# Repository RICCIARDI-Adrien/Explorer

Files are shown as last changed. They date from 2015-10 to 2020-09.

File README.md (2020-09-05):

# Explorer

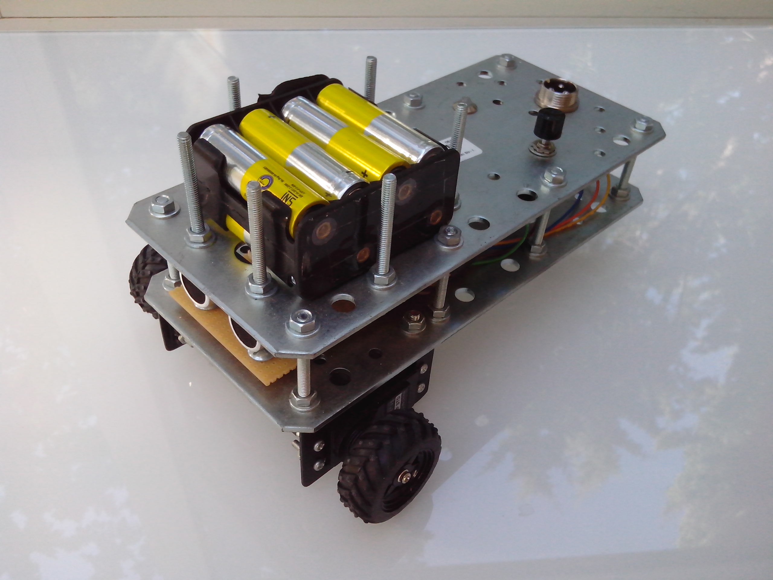
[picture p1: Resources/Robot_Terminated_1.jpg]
Robot terminated 1


A small wheeled robot based on a PIC18F26K22 microcontroller and a single ultrasonic distance sensor.  
The goal was to develop and test two basic artificial intelligence algorithms, both relying only on the ultrasonic sensor :
- The robot moves at will in a room and must avoid obstacles. It must never remain stuck.
- The robot is idle, waiting for a moving object to come close to it. Then, it must follow the moving object, staying at a safe distance. If the moving object comes too close from the robot, the robot must escape.

## Hardware
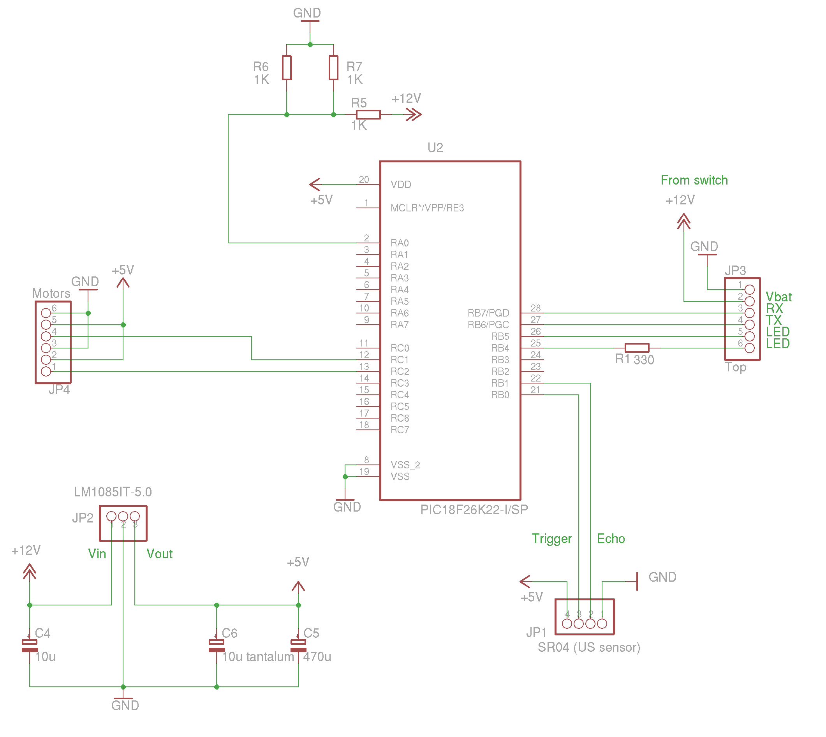
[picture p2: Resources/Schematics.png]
Main board schematics


## Build tools
The schematics and PCB were drawn using Cadsoft Eagle 6.6.0.  
The microcontroller firmware is built with SourceBoost 7.30.  
The Command Line Interface program can be built under Linux using gcc or under Windows with Cygwin or MinGW.

## Photo gallery

### Chassis construction

Start with two 200x90x2mm galvanized steel plates :
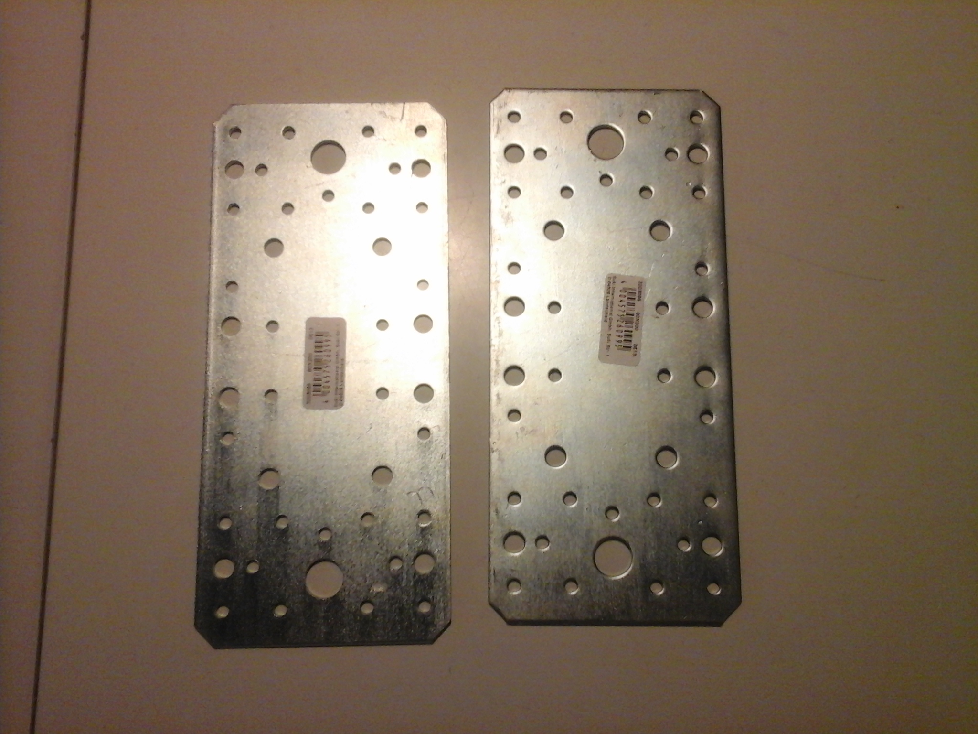
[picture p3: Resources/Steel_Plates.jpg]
Steel plates


One plate will be the chassis bottom. Make holes for servomotor support flat angle brackets and screw them :
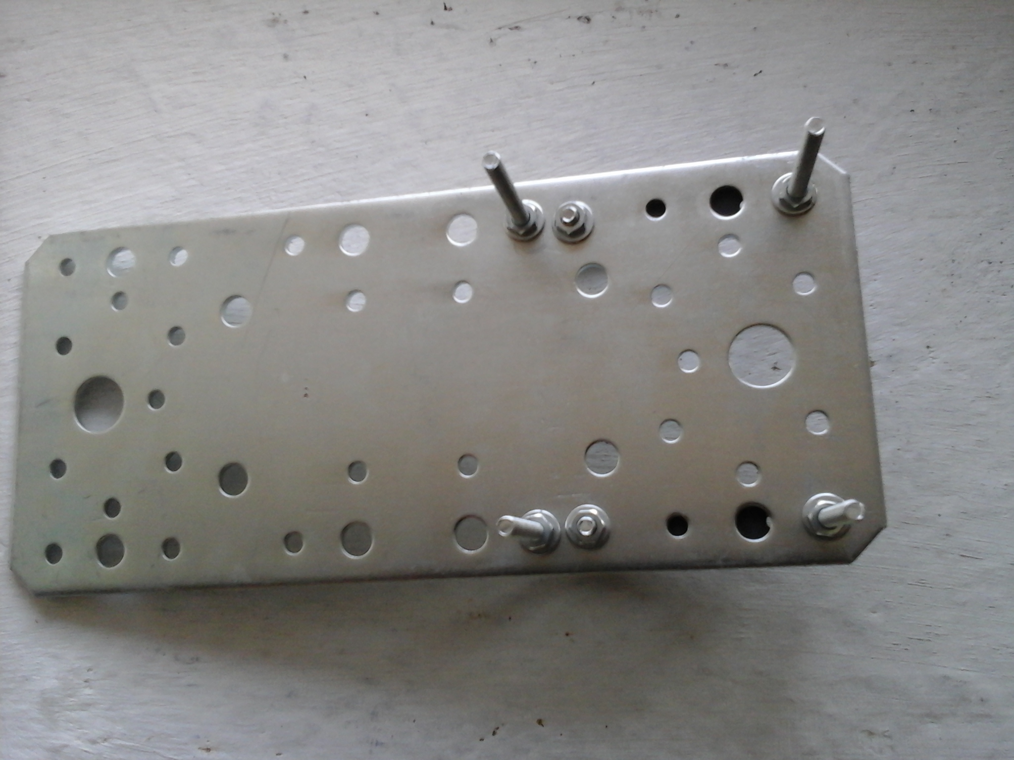
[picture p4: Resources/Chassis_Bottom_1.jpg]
Chassis bottom 1


Here is the other side :
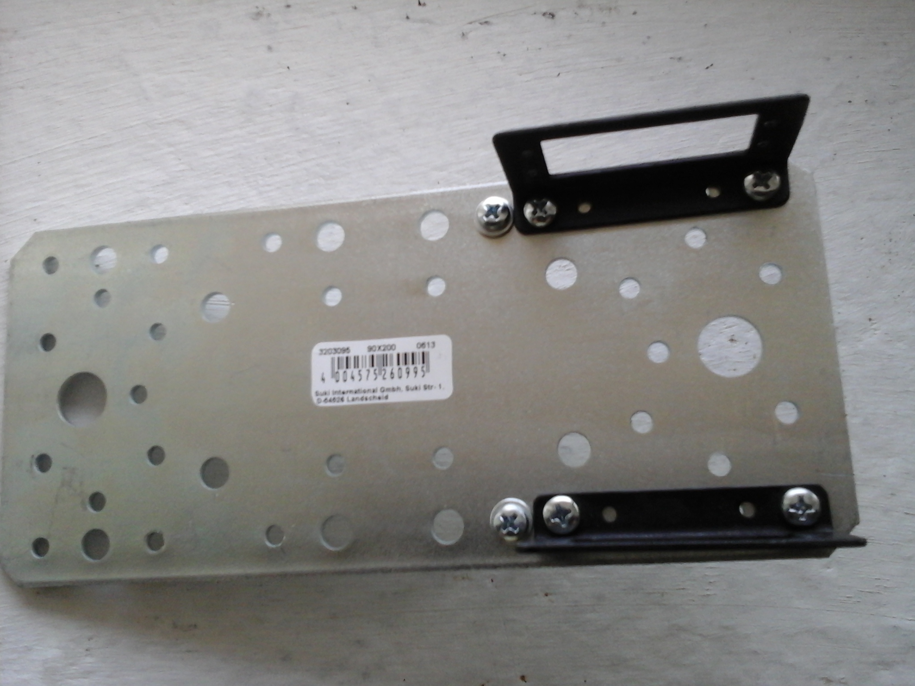
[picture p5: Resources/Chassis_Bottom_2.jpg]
Chassis bottom 2


Now screw the free wheel :
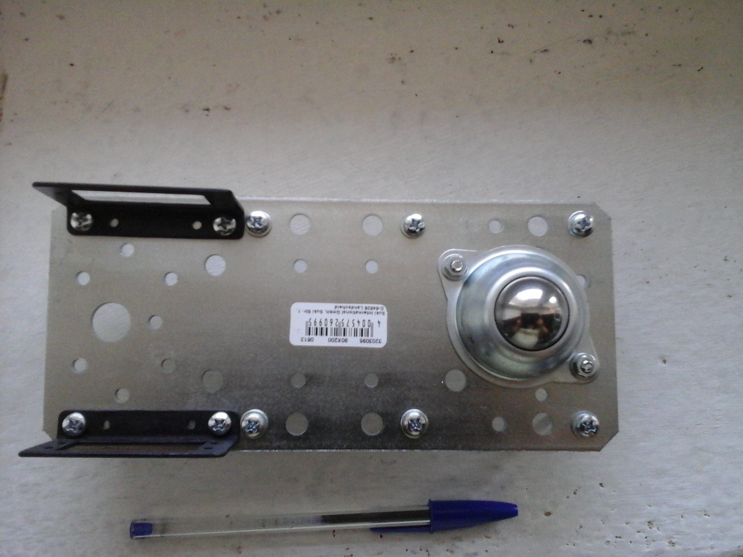
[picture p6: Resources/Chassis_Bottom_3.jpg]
Chassis bottom 3


Add the screws that will hold the chassis upper plate :
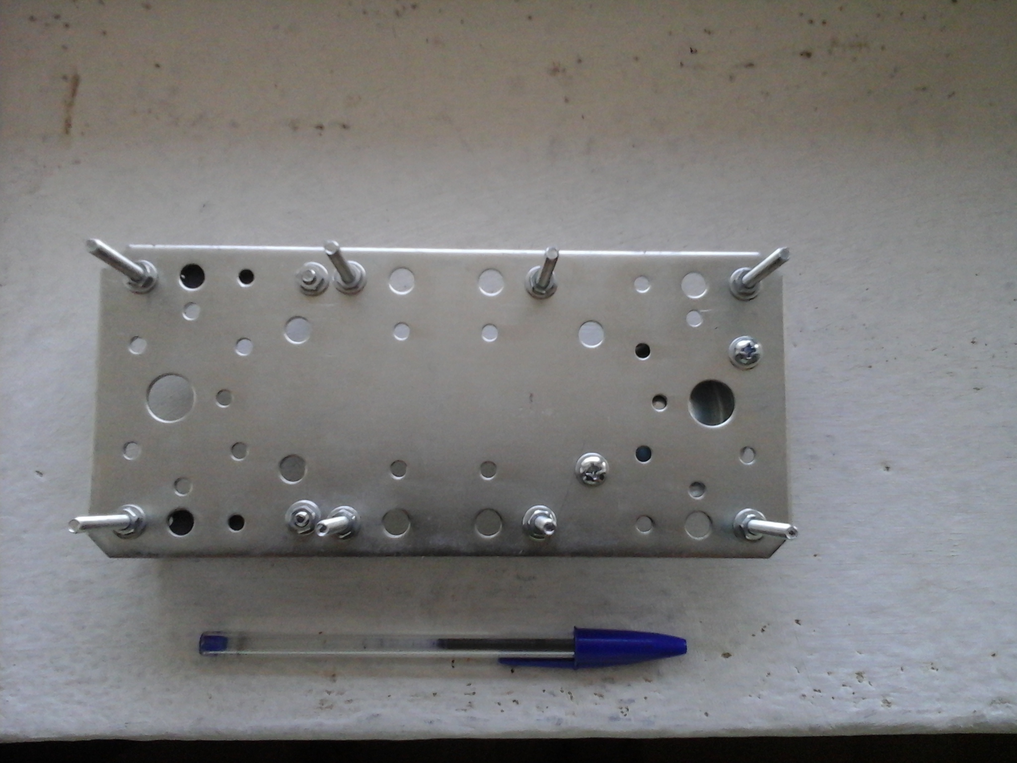
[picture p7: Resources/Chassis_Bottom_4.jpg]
Chassis bottom 4


### Motors assembly

Here are the servomotors :
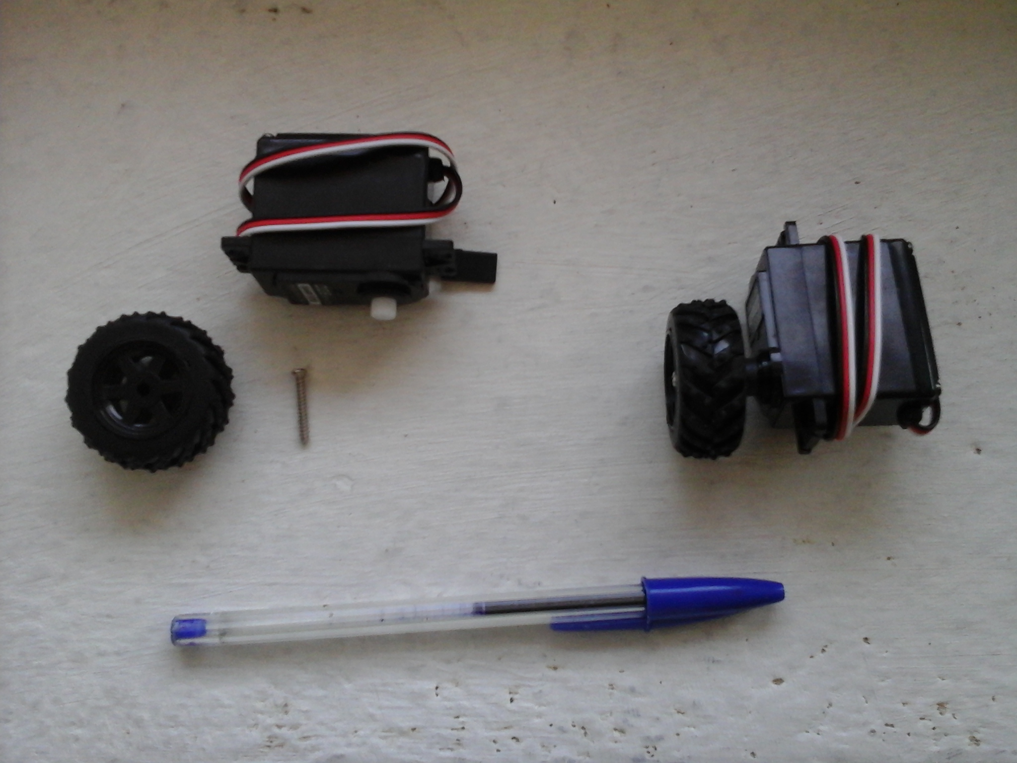
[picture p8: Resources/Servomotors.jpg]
Servomotors


Screw them into supports :
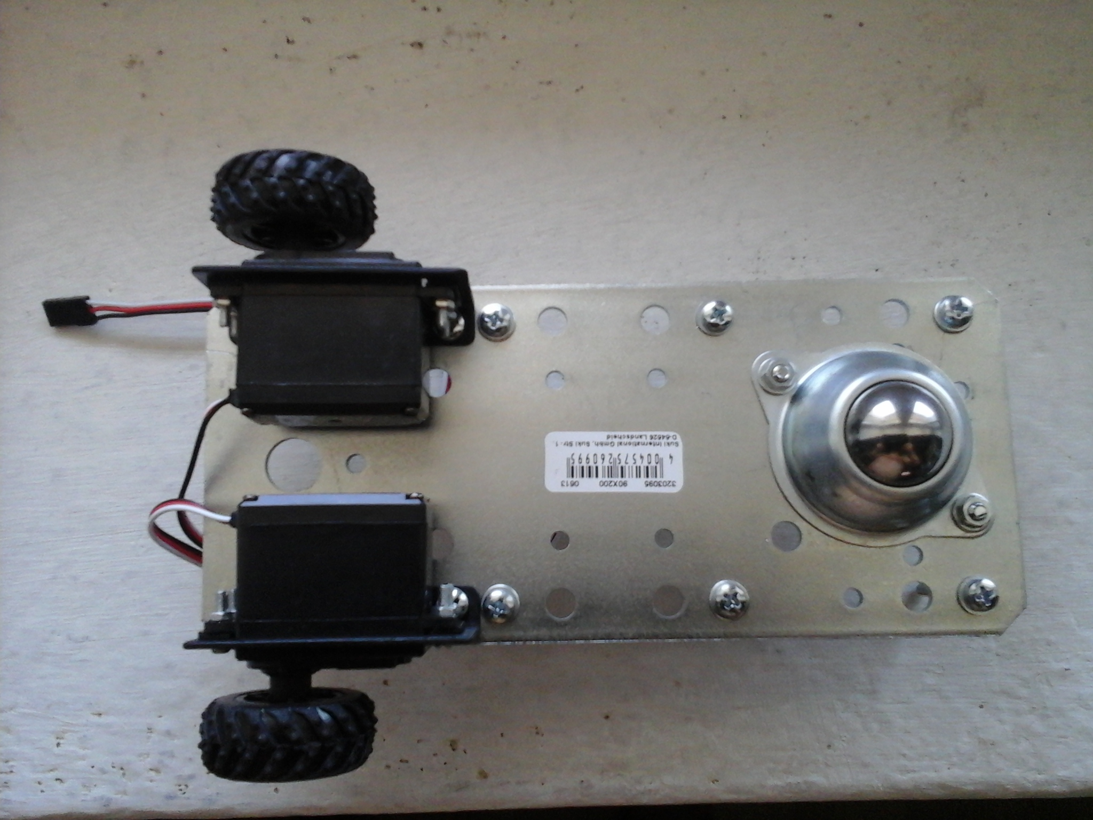
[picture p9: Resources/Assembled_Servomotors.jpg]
Assembled servomotors


### Voltage regulator assembly

Screw voltage regulator to chassis bottom plate. This allows to use the whole chassis as heat sink.
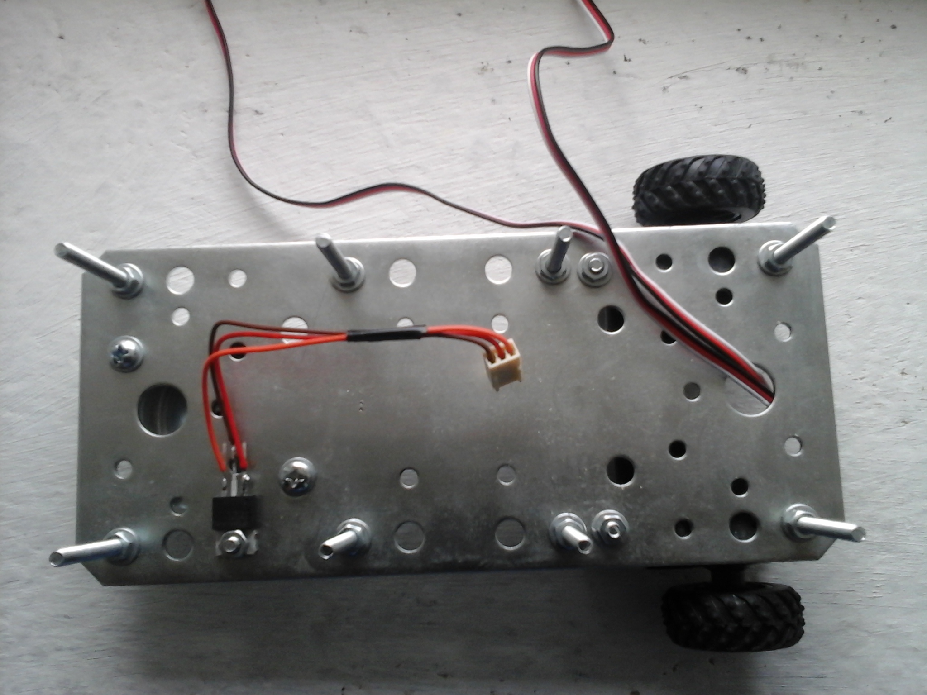
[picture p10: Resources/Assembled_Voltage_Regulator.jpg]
Assembled voltage regulator


### Chassis upper part

Drill holes for LED, switch and serial communication connector, then screw them. Also add the nuts and bolts that will hold the battery pack.
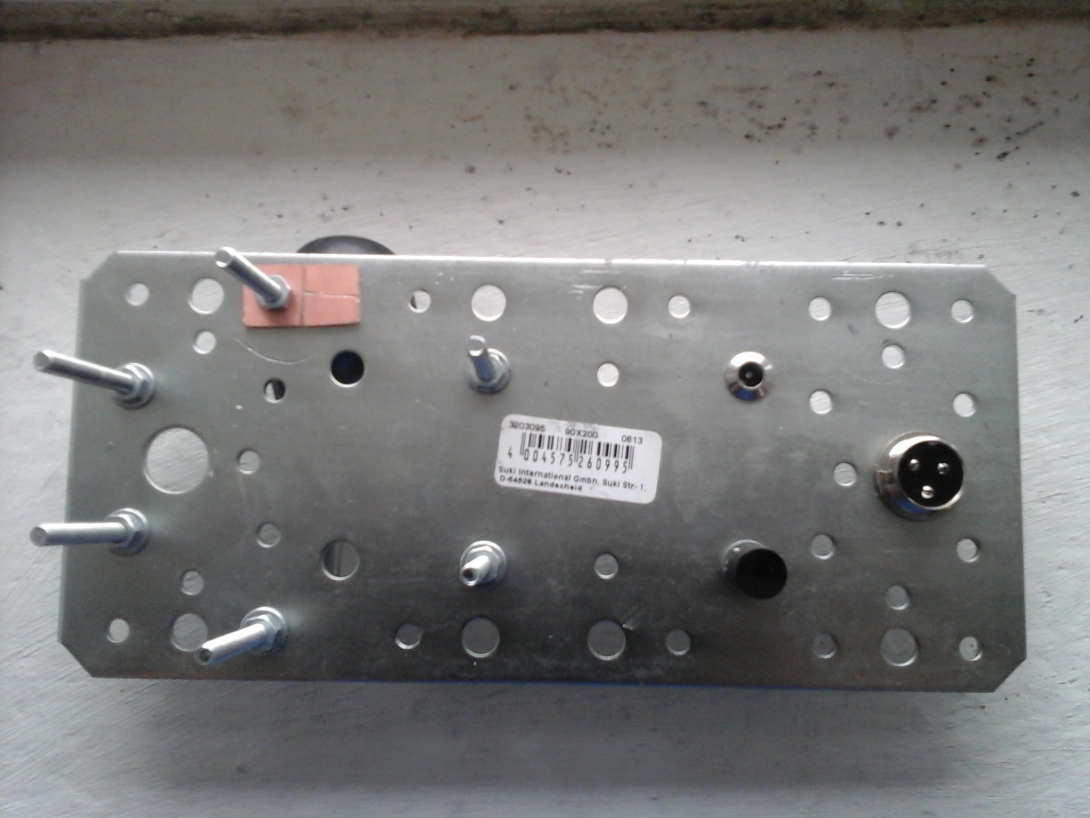
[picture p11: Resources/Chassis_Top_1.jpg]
Chassis top 1


Solder battery pack coupler to a little piece of PCB (don't forget to isolate terminals). This way, when coupler wires will break (it just a matter of time before it happens), it is easy to repair without having to disassemble the chassis.
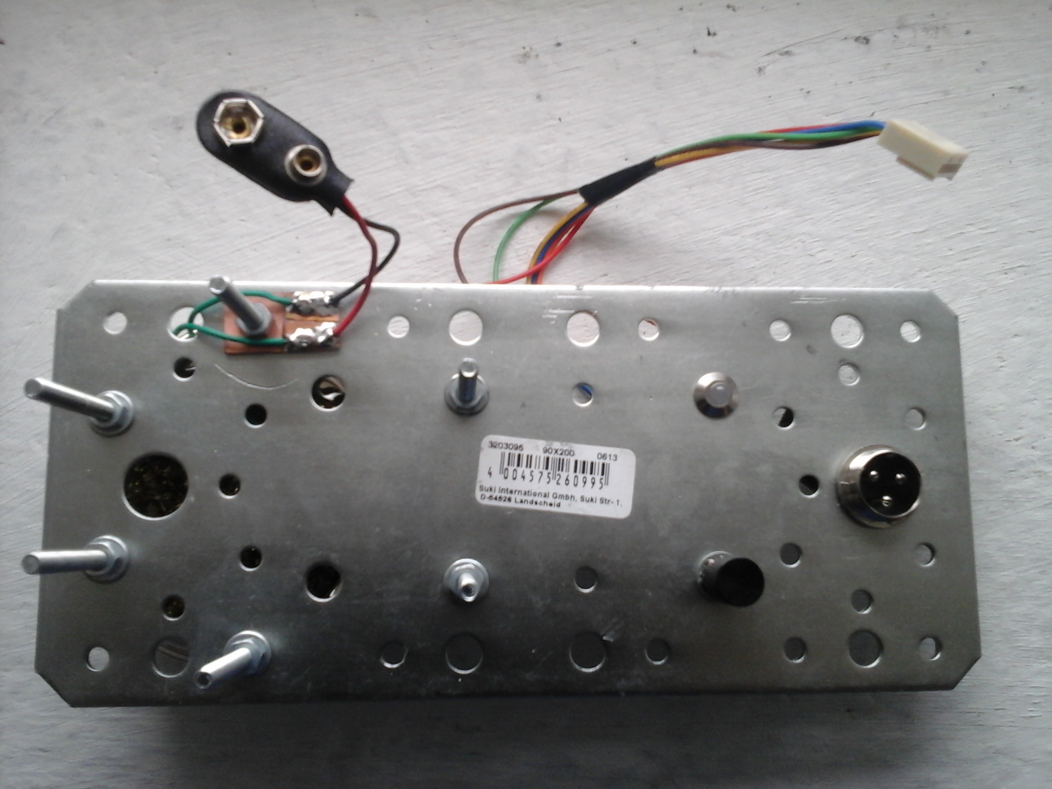
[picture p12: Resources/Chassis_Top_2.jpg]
Chassis top 2


Solder LED, switch and connector wires :
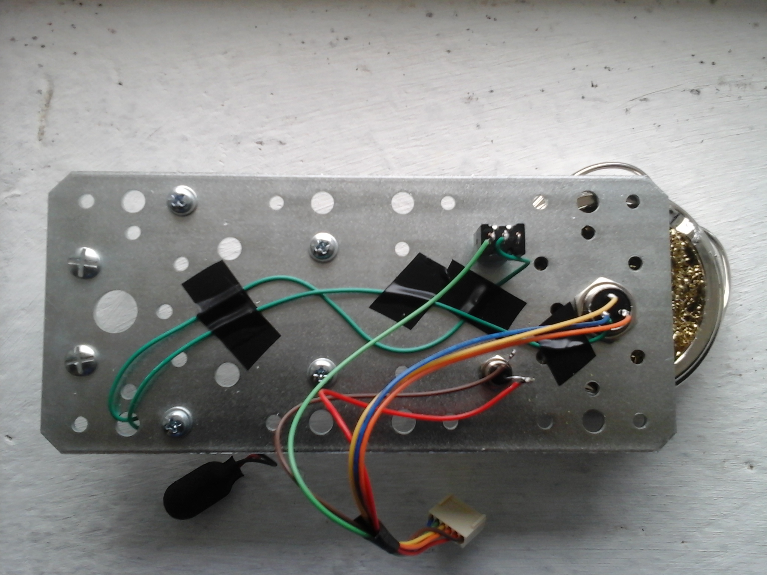
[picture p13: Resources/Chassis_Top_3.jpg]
Chassis top 3


### Electronic board

Board is made of test PCB soldered by hand.
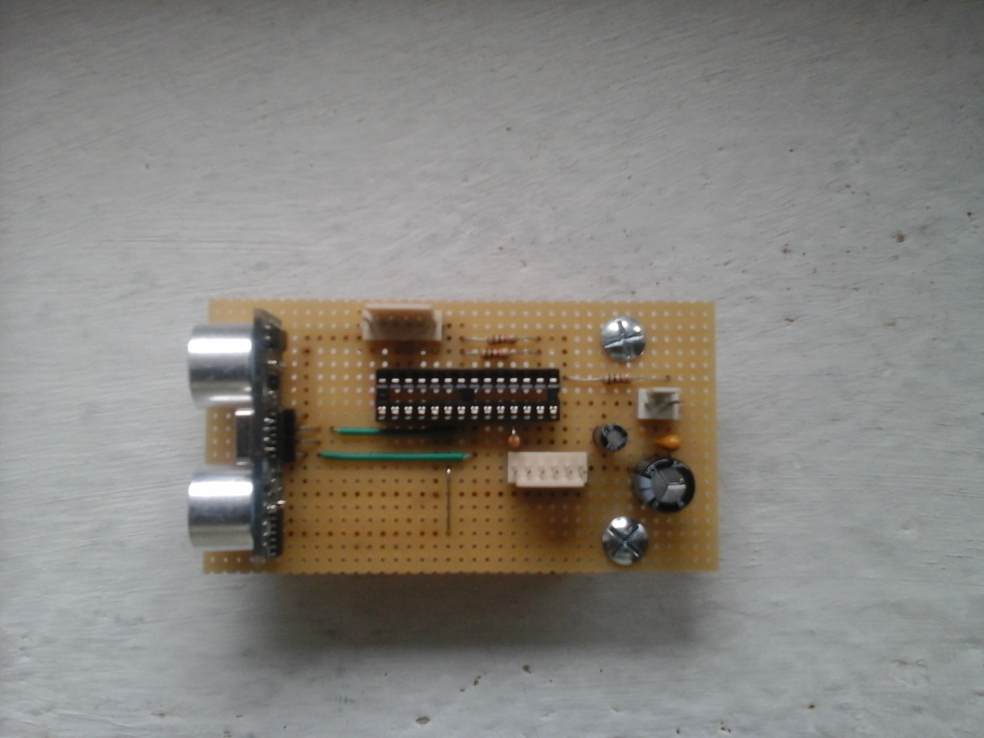
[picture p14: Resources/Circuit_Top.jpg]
Circuit top

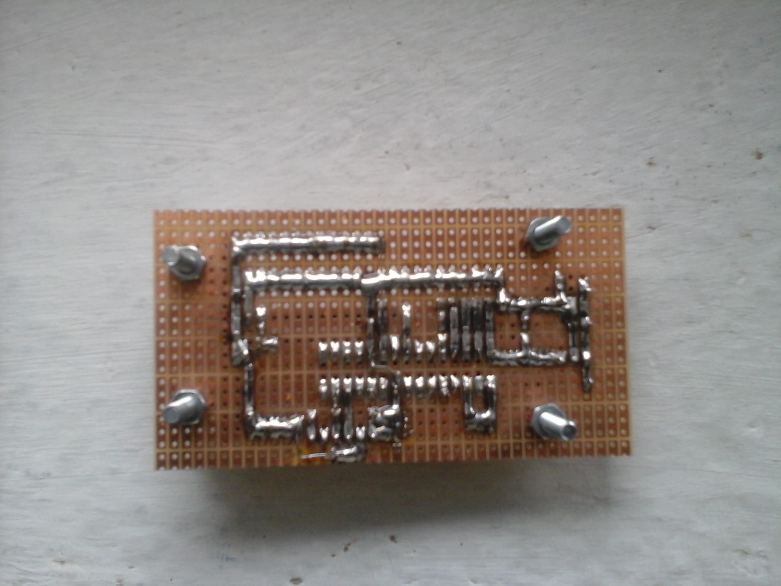
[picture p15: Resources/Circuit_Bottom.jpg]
Circuit bottom


Here is the board screwed to the chassis bottom :
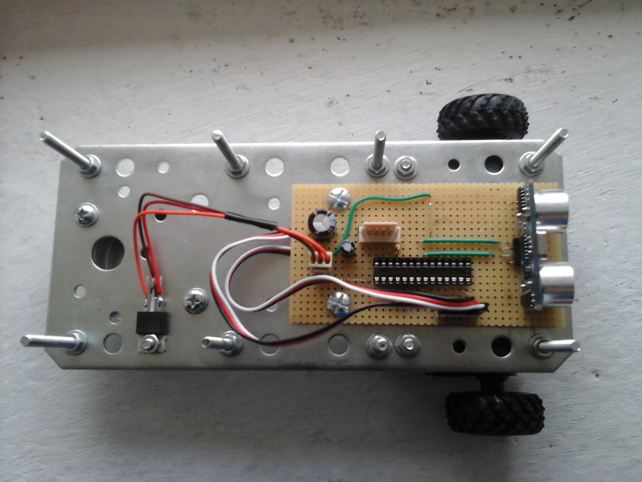
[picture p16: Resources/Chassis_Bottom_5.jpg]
Chassis bottom 5


### Fully assembled robot

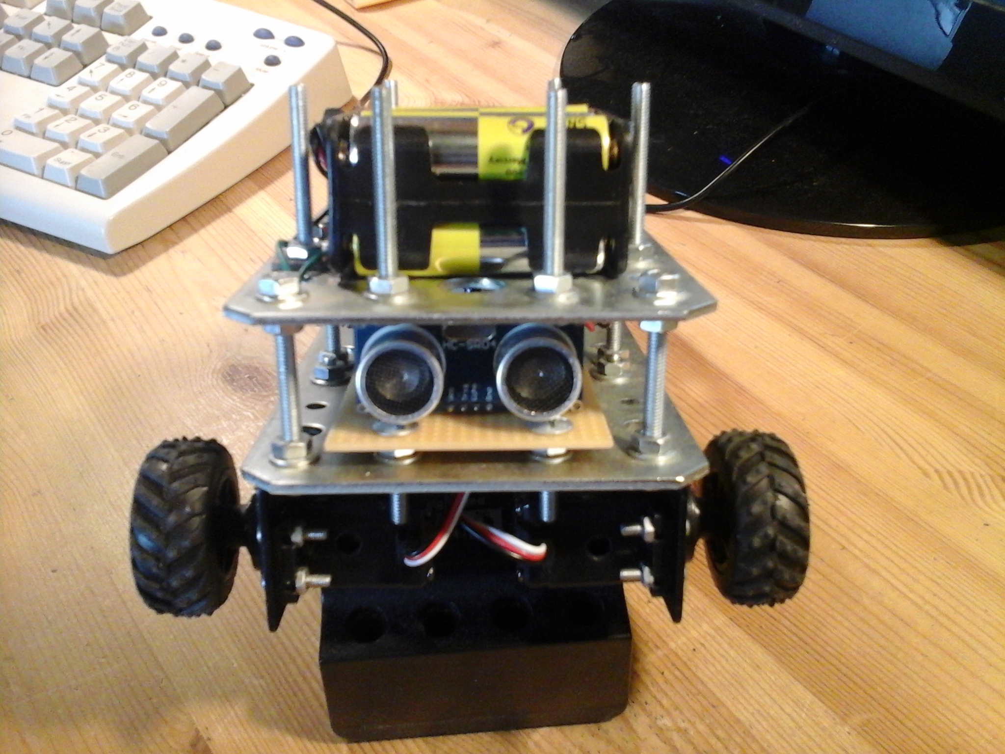
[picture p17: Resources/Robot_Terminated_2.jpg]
Robot terminated 2

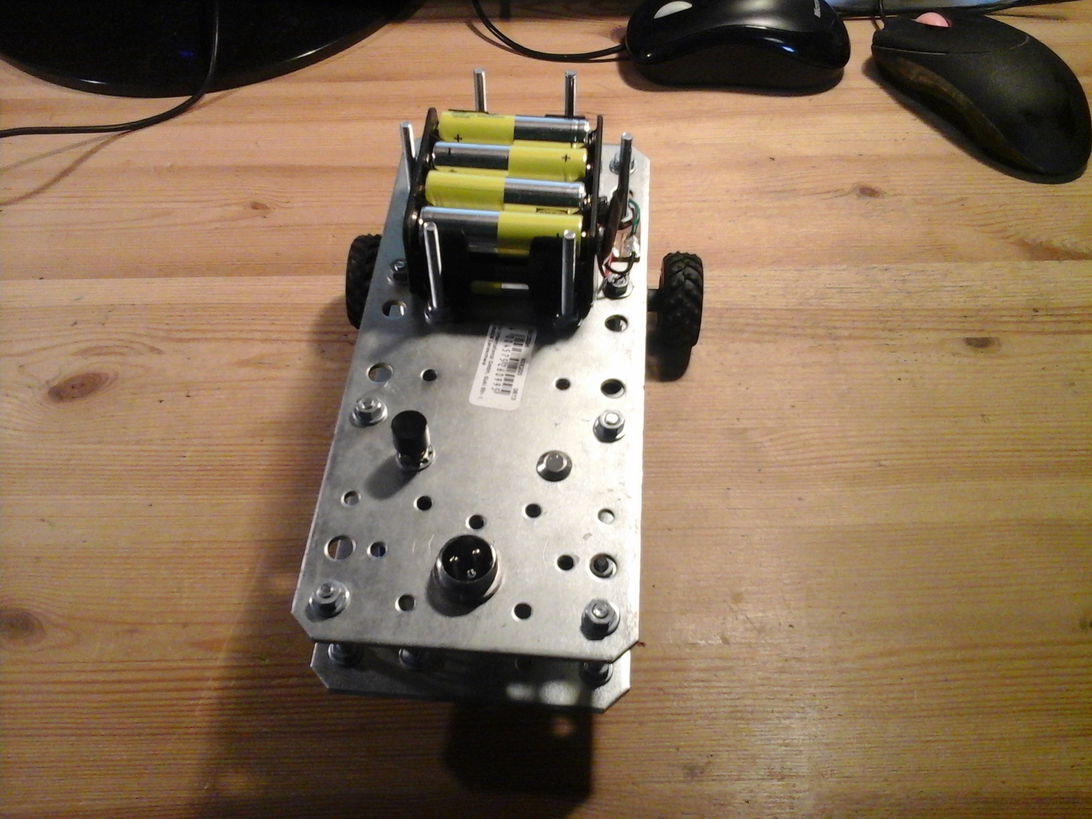
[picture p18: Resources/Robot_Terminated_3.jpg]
Robot terminated 3

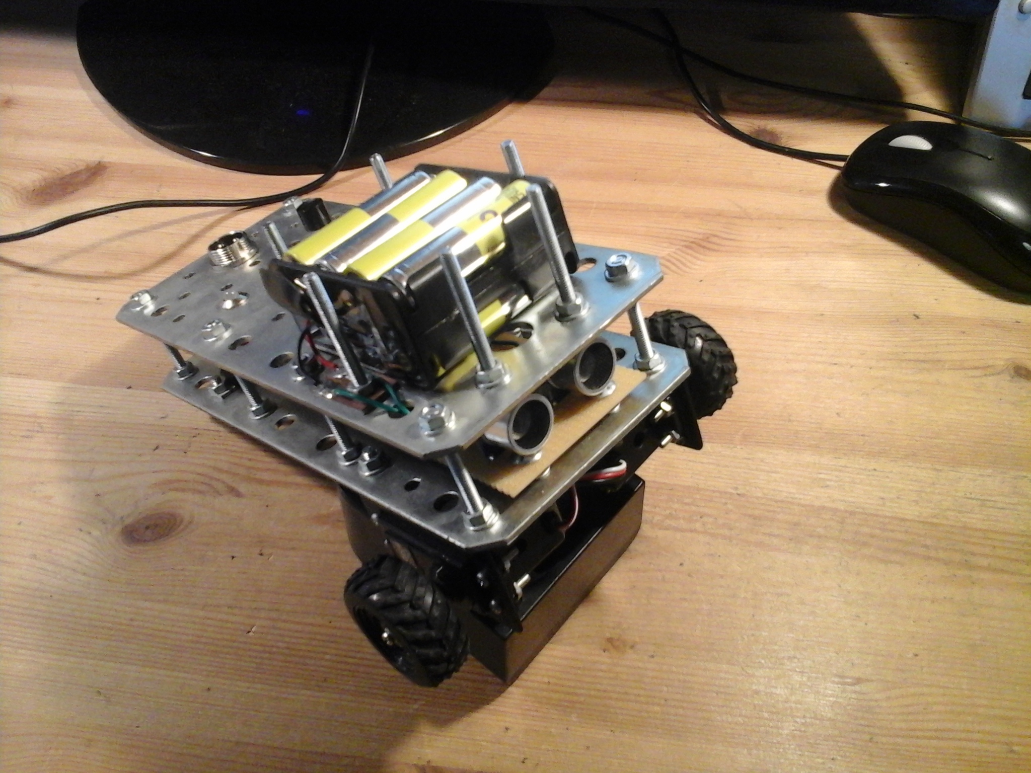
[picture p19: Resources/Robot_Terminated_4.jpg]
Robot terminated 4


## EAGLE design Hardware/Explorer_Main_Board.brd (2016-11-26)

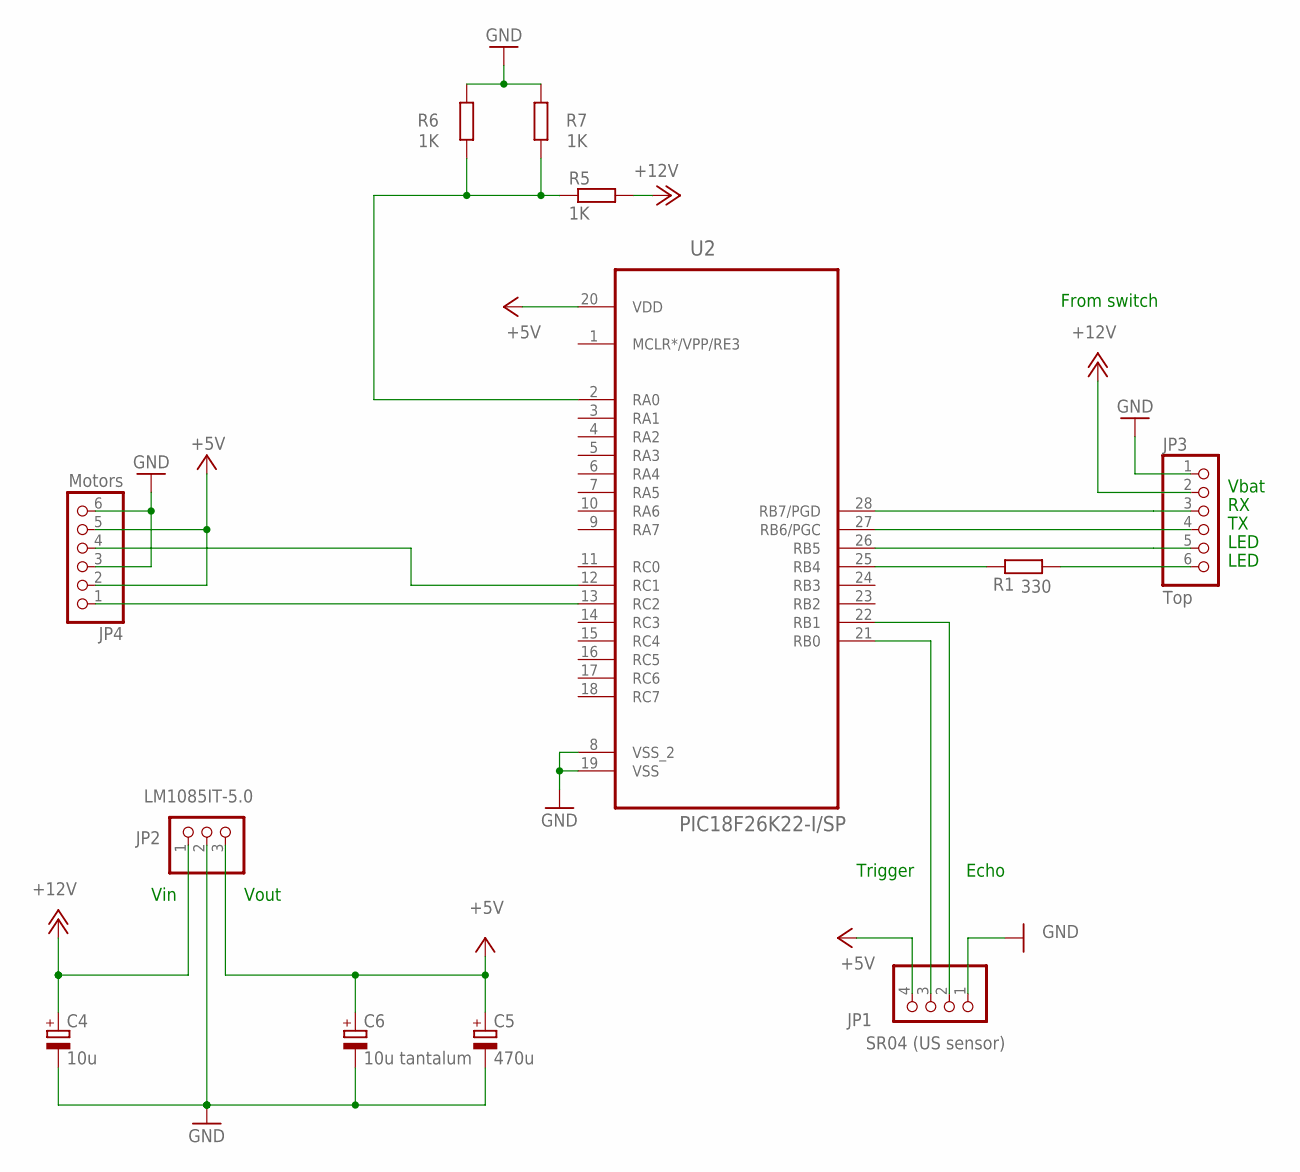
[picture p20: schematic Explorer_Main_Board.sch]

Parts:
C4: 10u; E2,5-6E
C5: 470u; E5-8,5
C6: 10u tantalum; E2,5-6E
JP1: SR04 (US sensor); 1X04
JP2: LM1085IT-5.0; 1X03
JP3: Top; 1X06
JP4: Motors; 1X06
R1: 330; 0207/12
R5, R6, R7: 1K; 0207/12
U2: PIC18F26K22-I/SP; DIP254P762X508-28P

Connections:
+5V: C5.+, C6.+, JP1.4, JP2.3, JP4.2, JP4.5, U2.20 (VDD)
+12V: C4.+, JP2.1, JP3.2, R5.2
GND: C4.-, C5.-, C6.-, JP1.1, JP2.2, JP3.1, JP4.3, JP4.6, R6.2, R7.2, U2.8 (VSS_2), U2.19 (VSS)
unnamed: JP3.6, R1.1
unnamed: R1.2, U2.25 (RB4)
unnamed: JP1.2, U2.22 (RB1)
unnamed: JP1.3, U2.21 (RB0)
unnamed: R5.1, R6.1, R7.1, U2.2 (RA0)
unnamed: JP3.3, U2.28 (RB7/PGD)
unnamed: JP3.4, U2.27 (RB6/PGC)
unnamed: JP4.4, U2.12 (RC1)
unnamed: JP4.1, U2.13 (RC2)
unnamed: JP3.5, U2.26 (RB5)

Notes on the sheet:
Vbat
From switch
LED
Vin
Vout
Echo
Trigger

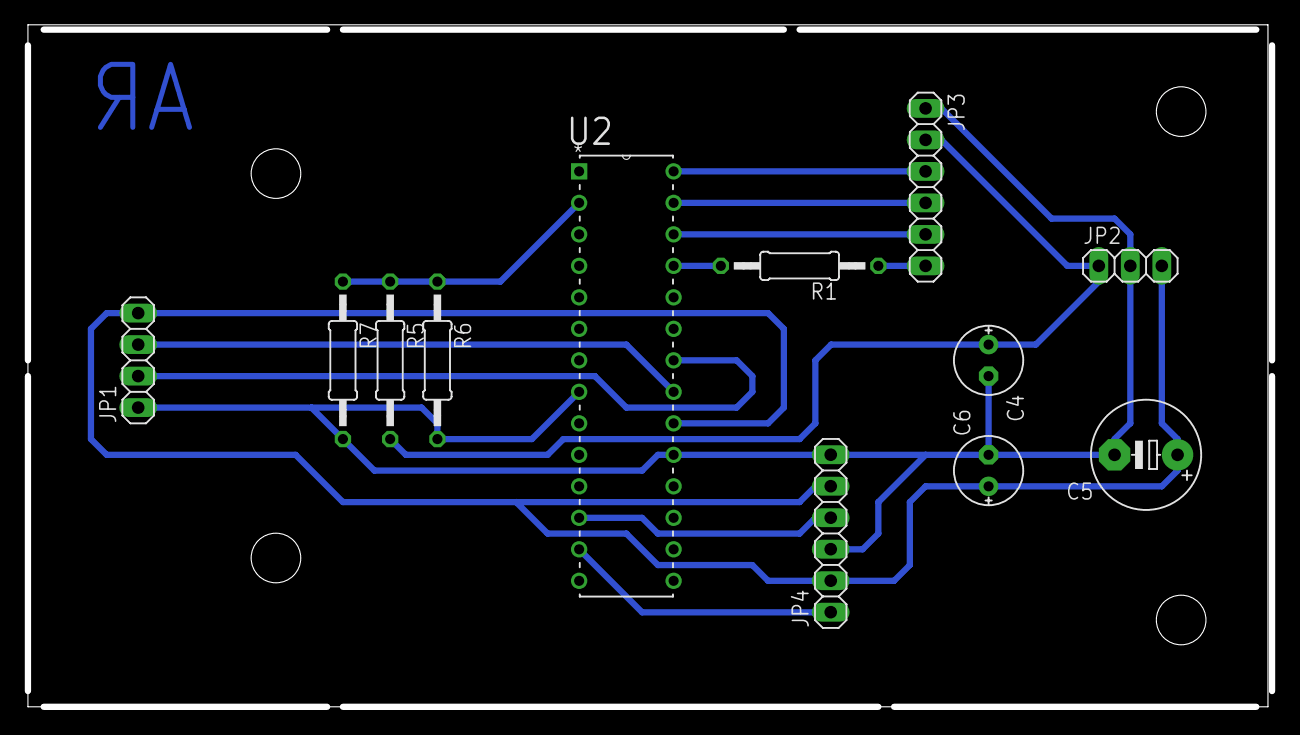
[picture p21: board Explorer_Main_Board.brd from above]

Board: 2 copper layers, 100.0 x 55.0 mm, 12 parts (0 on the bottom side), 13 nets.

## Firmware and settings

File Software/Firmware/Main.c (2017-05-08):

/** @file Main.c
 * Explorer robot artificial intelligence entry point and main loop.
 * @author Adrien RICCIARDI
 */
#include <system.h>
#include "ADC.h"
#include "Artificial_Intelligence.h"
#include "Distance_Sensor.h"
#include "Led.h"
#include "Motor.h"
#include "Random.h"
#include "Shared_Timer.h"
#include "UART.h"

//--------------------------------------------------------------------------------------------------
// Microcontroller configuration
//--------------------------------------------------------------------------------------------------
#pragma DATA _CONFIG1H, _IESO_OFF_1H & _FCMEN_OFF_1H & _PRICLKEN_ON_1H & _PLLCFG_ON_1H & _FOSC_INTIO67_1H // Disable oscillator switchover mode, disable fail-safe clock monitor, always enable primary clock, always enable PLL, select the internal oscillator block
#pragma DATA _CONFIG2L, _BORV_285_2L & _BOREN_SBORDIS_2L & _PWRTEN_ON_2L // Use the highest Brown-out reset voltage level, enable the Brown-out reset in hardware only, enable the Power-up timer
#pragma DATA _CONFIG2H, _WDTEN_OFF_2H // Disable the watchdog timer in hardware
#pragma DATA _CONFIG3H, _MCLRE_INTMCLR_3H & _HFOFST_OFF_3H & _PBADEN_OFF_3H & _CCP2MX_PORTC1_3H // Disable /MCLR, wait for the system clock to stabilize before starting the core, PORTB pins are configured as digital I/O, CCP2 is multiplexed with RC1
#pragma DATA _CONFIG4L, _DEBUG_OFF_4L & _XINST_OFF_4L & _LVP_OFF_4L & _STVREN_ON_4L // Disable the background debugger, disable the extended instruction set, disable the Single-supply ICSP, reset the MCU if a stack overflow/underflow occurs
#pragma DATA _CONFIG5L, _CP3_OFF_5L & _CP2_OFF_5L & _CP1_OFF_5L & _CP0_OFF_5L // Disable all code protections
#pragma DATA _CONFIG5H, _CPD_OFF_5H & _CPB_OFF_5H // Disable the data EEPROM and the Boot block code protections
#pragma DATA _CONFIG6L, _WRT3_OFF_6L & _WRT2_OFF_6L & _WRT1_OFF_6L & _WRT0_OFF_6L // Disable all write protections
#pragma DATA _CONFIG6H, _WRTD_OFF_6H & _WRTB_OFF_6H & _WRTC_OFF_6H // Disable data EEPROM, Boot block and configuration registers write protection
#pragma DATA _CONFIG7L, _EBTR3_OFF_7L & _EBTR2_OFF_7L & _EBTR1_OFF_7L & _EBTR0_OFF_7L // Disable all table read protections
#pragma DATA _CONFIG7H, _EBTRB_OFF_7H // Disable Boot block table read protection

// Configure clock frequency
#pragma CLOCK_FREQ 64000000

//--------------------------------------------------------------------------------------------------
// Entry point
//--------------------------------------------------------------------------------------------------
void main(void)
{
	// Initialize the peripherals (there is no need to initialize the clock as the bootloader already did)
	UARTInitialize();
	ADCInitialize();
	DistanceSensorInitialize();
	MotorInitialize();
	SharedTimerInitialize();
	LedInitialize();
	RandomInitialize();
	
	// Enable the interrupts
	rcon.IPEN = 1; // Enable interrupt priority
	intcon |= 0xC0; // Enable all high priority and all low priority interrupts
	
	// Stop the motors
	MotorSetState(MOTOR_LEFT, MOTOR_STATE_STOPPED);
	MotorSetState(MOTOR_RIGHT, MOTOR_STATE_STOPPED);
	
	// Wait enough time to let the distance sensor sample a real value
	delay_ms(120);
	
	// System is ready
	LedOnGreen();
	
	while (1)
	{
		//ArtificialIntelligenceAvoidObjects();
		ArtificialIntelligenceFollowObjects();
	}
}

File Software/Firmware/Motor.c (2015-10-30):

/** @file Motor.c
 * @see Motor.h for description.
 * @author Adrien RICCIARDI
 */
#include <system.h>
#include "Motor.h"

//--------------------------------------------------------------------------------------------------
// Private constants and macros
//--------------------------------------------------------------------------------------------------
// PWM pins
#define MOTOR_LEFT_PIN 2
#define MOTOR_RIGHT_PIN 1

// The motors duty cycles
#define MOTOR_LEFT_FORWARD_DUTY_CYCLE (MOTOR_MAXIMUM_DUTY_CYCLE_VALUE - MOTOR_MINIMUM_DUTY_CYCLE_VALUE + 2000)
#define MOTOR_LEFT_BACKWARD_DUTY_CYCLE (MOTOR_MAXIMUM_DUTY_CYCLE_VALUE - MOTOR_MINIMUM_DUTY_CYCLE_VALUE + 4000)
#define MOTOR_RIGHT_FORWARD_DUTY_CYCLE (MOTOR_MAXIMUM_DUTY_CYCLE_VALUE - MOTOR_MINIMUM_DUTY_CYCLE_VALUE + 4000)
#define MOTOR_RIGHT_BACKWARD_DUTY_CYCLE (MOTOR_MAXIMUM_DUTY_CYCLE_VALUE - MOTOR_MINIMUM_DUTY_CYCLE_VALUE + 2000)

// PWM hardware limits
/** The 0% duty cycle value. */
#define MOTOR_MINIMUM_DUTY_CYCLE_VALUE 40000 // = (Fosc/4)/(prescaler*50Hz)
/** The 100% duty cycle value. */
#define MOTOR_MAXIMUM_DUTY_CYCLE_VALUE 65535
/** Make the timer 1 overflows each 50Hz. */
#define MOTOR_PWM_TIMER_RELOAD_VALUE (MOTOR_MAXIMUM_DUTY_CYCLE_VALUE - MOTOR_MINIMUM_DUTY_CYCLE_VALUE)
/** Enable the timer 1. */
#define MOTOR_PWM_TIMER_START() t1con.TMR1ON = 1
/** Disable the timer 1. */
#define MOTOR_PWM_TIMER_STOP() t1con.TMR1ON = 0

/** How many motors to handle. */
#define MOTORS_COUNT 2

//--------------------------------------------------------------------------------------------------
// Private variables
//--------------------------------------------------------------------------------------------------
/** Each motor current duty cycle. */
static unsigned short Motor_Current_Duty_Cycle[MOTORS_COUNT];

//--------------------------------------------------------------------------------------------------
// Public functions
//--------------------------------------------------------------------------------------------------
void MotorInitialize(void)
{
	// Configure the pins as digital
	anselc.MOTOR_LEFT_PIN = 0;
	anselc.MOTOR_RIGHT_PIN = 0;
	// Configure PWM pins as outputs
	trisc.MOTOR_LEFT_PIN = 0;
	trisc.MOTOR_RIGHT_PIN = 0;
	
	// Stop motors
	portc.MOTOR_LEFT_PIN = 0;
	portc.MOTOR_RIGHT_PIN = 0;
	
	// Configure the CCP modules in Compare mode
	ccp1con = 0x0A;
	ccp2con = 0x0A;
	ccptmrs0 = 0; // Use timer 1 as clock source for both compare modules
	ipr1.CCP1IP = 0; // Set both interrupts as low priority
	ipr2.CCP2IP = 0;
	
	// Configure the timer 1 to generate a 50Hz frequency
	tmr1h = MOTOR_PWM_TIMER_RELOAD_VALUE >> 8;
	tmr1l = (unsigned char) MOTOR_PWM_TIMER_RELOAD_VALUE;
	t1con = 0x33; // Use Fosc/4 as clock source, use a 8x prescaler, disable the dedicated secondary oscillator circuit, access to the timer registers in one 16-bit operation, enable the timer
	ipr1.TMR1IP = 0; // Set the timer 1 as a low priority interrupt
	pie1.TMR1IE = 1; // Enable the timer 1 interrupt	
}

void MotorInterruptHandler(void)
{
	MOTOR_PWM_TIMER_STOP();

	// Handle timer 1 overflow : the PWM period is over
	if (pir1.TMR1IF)
	{
		// Update the left motor duty cycle
		// Schedule an interrupt if the left motor duty cycle is in range ]0;100%[
		if ((Motor_Current_Duty_Cycle[MOTOR_LEFT] > 0) && (Motor_Current_Duty_Cycle[MOTOR_LEFT] < MOTOR_MAXIMUM_DUTY_CYCLE_VALUE))
		{
			// Update the left motor PWM duty cycle
			ccpr1h = Motor_Current_Duty_Cycle[MOTOR_LEFT] >> 8;
			ccpr1l = (unsigned char) Motor_Current_Duty_Cycle[MOTOR_LEFT];
			pie1.CCP1IE = 1;
		}
		else pie1.CCP1IE = 0;
		// Set the pin state
		if (Motor_Current_Duty_Cycle[MOTOR_LEFT] == 0) portc.MOTOR_LEFT_PIN = 0;
		else portc.MOTOR_LEFT_PIN = 1;
		
		// Update the right motor duty cycle
		// Schedule an interrupt if the right motor duty cycle is in range ]0;100%[
		if ((Motor_Current_Duty_Cycle[MOTOR_RIGHT] > 0) && (Motor_Current_Duty_Cycle[MOTOR_RIGHT] < MOTOR_MAXIMUM_DUTY_CYCLE_VALUE))
		{
			// Update the right motor PWM duty cycle
			ccpr2h = Motor_Current_Duty_Cycle[MOTOR_RIGHT] >> 8;
			ccpr2l = (unsigned char) Motor_Current_Duty_Cycle[MOTOR_RIGHT];
			pie2.CCP2IE = 1;
		}
		else pie2.CCP2IE = 0;
		// Set the pin state
		if (Motor_Current_Duty_Cycle[MOTOR_RIGHT] == 0) portc.MOTOR_RIGHT_PIN = 0;
		else portc.MOTOR_RIGHT_PIN = 1;
	
		// Reload the timer
		tmr1h = MOTOR_PWM_TIMER_RELOAD_VALUE >> 8;
		tmr1l = (unsigned char) MOTOR_PWM_TIMER_RELOAD_VALUE;
		
		// Reset the interrupt flag
		pir1.TMR1IF = 0;
	}
	
	// Handle the CCP1 interrupt : the left motor pin must change state
	if ((pie1.CCP1IE) && (pir1.CCP1IF))
	{
		portc.MOTOR_LEFT_PIN = 0;
		
		// Reset interrupt flag
		pir1.CCP1IF = 0;
	}
	
	// Handle the CCP2 interrupt : the right motor pin must change state
	if ((pie2.CCP2IE) && (pir2.CCP2IF))
	{
		portc.MOTOR_RIGHT_PIN = 0;
		
		// Reset interrupt flag
		pir2.CCP2IF = 0;
	}
	
	MOTOR_PWM_TIMER_START();
}

void MotorSetState(TMotor Motor, TMotorState State)
{
	MOTOR_PWM_TIMER_STOP();
	
	// Choose the right duty cycle according to selected state
	switch (State)
	{
		case MOTOR_STATE_STOPPED:
			Motor_Current_Duty_Cycle[Motor] = 0;
			break;
			
		case MOTOR_STATE_FORWARD:
			if (Motor == MOTOR_LEFT) Motor_Current_Duty_Cycle[MOTOR_LEFT] = MOTOR_LEFT_FORWARD_DUTY_CYCLE;
			else Motor_Current_Duty_Cycle[MOTOR_RIGHT] = MOTOR_RIGHT_FORWARD_DUTY_CYCLE;
			break;
			
		case MOTOR_STATE_BACKWARD:
			if (Motor == MOTOR_LEFT) Motor_Current_Duty_Cycle[MOTOR_LEFT] = MOTOR_LEFT_BACKWARD_DUTY_CYCLE;
			else Motor_Current_Duty_Cycle[MOTOR_RIGHT] = MOTOR_RIGHT_BACKWARD_DUTY_CYCLE;
			break;
	}
		
	MOTOR_PWM_TIMER_START();
}

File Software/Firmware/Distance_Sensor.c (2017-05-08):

/** @file Distance_Sensor.c
 * @see Distance_Sensor.h for description.
 * @author Adrien RICCIARDI
 */
#include <system.h>
#include "Distance_Sensor.h"

//--------------------------------------------------------------------------------------------------
// Private constants and macros
//--------------------------------------------------------------------------------------------------
/** The "trigger" pin. */
#define DISTANCE_SENSOR_TRIGGER_PIN 0 // RB0
/** The "echo" pin. */
#define DISTANCE_SENSOR_ECHO_PIN 1 // RB1

/** Start the counter. */
#define DISTANCE_SENSOR_COUNTER_TIMER_START() t0con.TMR0ON = 1
/** Stop the counter. */
#define DISTANCE_SENSOR_COUNTER_TIMER_STOP() t0con.TMR0ON = 0
/** Reset the counter. */
#define DISTANCE_SENSOR_COUNTER_TIMER_RESET() \
{ \
	tmr0h = 0; \
	tmr0l = 0; \
}

/** Enable the INT1 interrupt. */
#define DISTANCE_SENSOR_EXTERNAL_INTERRUPT_ENABLE() intcon3.INT1IE = 1
/** Disable the INT1 interrupt. */
#define DISTANCE_SENSOR_EXTERNAL_INTERRUPT_DISABLE() intcon3.INT1IE = 0

//--------------------------------------------------------------------------------------------------
// Private variables
//--------------------------------------------------------------------------------------------------
/** The distance to the nearest object in centimeters. */
static unsigned short Distance_Sensor_Last_Measured_Distance = 0; // Do not allow the motors to move until a real measure has been done

//--------------------------------------------------------------------------------------------------
// Public functions
//--------------------------------------------------------------------------------------------------
void DistanceSensorInitialize(void)
{
	// Configure the pins as digital
	anselb.DISTANCE_SENSOR_TRIGGER_PIN = 0;
	anselb.DISTANCE_SENSOR_ECHO_PIN = 0;
	
	// Configure the pins direction
	latb.DISTANCE_SENSOR_TRIGGER_PIN = 0; // Avoid triggering a spurious measure
	trisb.DISTANCE_SENSOR_TRIGGER_PIN = 0; // Set as output
	trisb.DISTANCE_SENSOR_ECHO_PIN = 1; // Set as input
	
	// Configure the timer 0 to increment every microsecond
	t0con = 0x03; // Enable the timer in 16-bit mode, use Fosc/4 as clock source, use a 1:16 prescaler, do not start the timer
	DISTANCE_SENSOR_COUNTER_TIMER_RESET();
	
	// Configure the external interrupt 1
	intcon2.INTEDG1 = 1; // Trigger an interrupt when a rising edge is detected
	intcon3.INT1IP = 1; // Set the interrupt as high priority
	DISTANCE_SENSOR_EXTERNAL_INTERRUPT_ENABLE();
	
	// Configure the timer 2 (this timer releases the trigger pin without using a busy loop in the interrupt handler)
	pr2 = 20; // The timer period is 1us, the recommended trigger pin hold time is 10us, so use 20us for increased safety
	ipr1.TMR2IP = 0; // Set the interrupt as low priority
	pie1.TMR2IE = 1; // Enable the interrupt
}

void DistanceSensorStartMeasure(void)
{
	// Trigger a distance measure
	latb.DISTANCE_SENSOR_TRIGGER_PIN = 1;
	// Configure timer 2 to trigger an interrupt 20us later
	tmr2 = 0;
	t2con = 0x06; // Do not use a postscaler, enable the timer, set a 16x prescaler to get a timer frequency of 1MHz (so it is easy to count microseconds)
}

unsigned short DistanceSensorGetLastSampledDistance(void)
{
	unsigned short Distance;
	
	// Atomically access to the shared variable
	DISTANCE_SENSOR_EXTERNAL_INTERRUPT_DISABLE();
	Distance = Distance_Sensor_Last_Measured_Distance;
	DISTANCE_SENSOR_EXTERNAL_INTERRUPT_ENABLE();
	
	return Distance;
}

void DistanceSensorInterruptHandler(void)
{
	static unsigned char Is_Waiting_For_Rising_Edge = 1; // The echo signal starts with a rising edge
	
	// A rising edge has been detected
	if (Is_Waiting_For_Rising_Edge)
	{
		DISTANCE_SENSOR_COUNTER_TIMER_START(); // Start counting
		intcon2.INTEDG1 = 0; // Configure the external interrupt to trigger an interrupt when a falling edge is detected
		Is_Waiting_For_Rising_Edge = 0;
	}
	// A falling edge has been detected
	else
	{
		DISTANCE_SENSOR_COUNTER_TIMER_STOP(); // Stop counting
		intcon2.INTEDG1 = 1; // Configure the external interrupt to trigger an interrupt when a rising edge is detected
		Is_Waiting_For_Rising_Edge = 1;
		
		// Retrieve the measured time
		Distance_Sensor_Last_Measured_Distance = tmr0l; // TMR0L must be read before TMR0H to grant a valid result
		Distance_Sensor_Last_Measured_Distance |= tmr0h << 8;
		DISTANCE_SENSOR_COUNTER_TIMER_RESET();
	}
	
	// Clear the interrupt flag
	intcon3.INT1IF = 0;
}

void DistanceSensorTriggerPinInterruptHandler(void)
{
	// Stop the timer
	t2con.TMR2ON = 0;
	
	// Release the trigger pin
	latb.DISTANCE_SENSOR_TRIGGER_PIN = 0;
	
	// Clear the interrupt flag
	pir1.TMR2IF = 0;
}

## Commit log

2015-07-19 Added schematics and PCB.
    [Explorer_Main_Board.brd, Explorer_Main_Board.sch]
2015-09-28 Added the bootloader and the firmware source directories. The firmware interrupt-driven UART is working.
2015-09-29 Added the battery voltage sampling code.
2015-10-07 The bootloader and the firmware update tool are working.
    [Configuration.h]
2015-10-07 Improved the update tool to a command line interface handling all the robot features.
    [Configuration.h]
2015-10-10 Added a detection of the currently running program (bootloader or firmware) to make the upgrading command fully automatic.
    [Configuration.h]
2015-10-11 Motors are working.
2015-10-11 Distance sensor is working.
2015-10-30 Improved the UART code and adapted it to the new bootloader.
2015-10-30 Reorganized some motors initialization intructions into a more coherent order.
2015-10-30 Force the shared timer to immediately trigger an interrupt in order to fastly sample a distance value.
2015-10-30 Added a timer to handle the distance sensor trigger pin.
2015-10-30 Added the 'avoid obstacles' IA behaviour.
    [Artificial_Intelligence.c, Main.c]
2015-10-30 Added a weak battery protection code.
2015-10-31 Improved the 'avoid obstacles' IA. The robot turns faster and is now able to go backward if the detected obstacles are too close.
    [Artificial_Intelligence.c]
2015-11-03 Improved the distance sensor sampling time.
2015-11-07 Added a new IA that avoids objects by turning randomly to left or right and a pseudo-random number generator.
    [Artificial_Intelligence.c, Main.c]
2015-11-14 Improved the 'avoid objects by randomly turning' AI.
    [Artificial_Intelligence.c]
2015-12-29 Added several software timers instead of only a single one.
2015-12-29 Added a delayed mechanism to the AI that avoids the objects by randomly turning which makes the robot come nearer to the obstacles while it is not scared by the obstacle proximity.
    [Artificial_Intelligence.c, Main.c]
2015-12-30 The robot can now choose between 4 angles when turning to avoid an obstacle.
    [Artificial_Intelligence.c]
2016-11-26 Replaced the Command Line Interface tool internal UART library by a git sub-module of the Serial Port library to keep it up to date.
    [Main.c]
2016-11-26 Updated Eagle project to Eagle 7.5.0 and improved schematics names displaying.
    [Explorer_Main_Board.brd, Explorer_Main_Board.sch]
2016-11-26 Displayed the schematics on the README.
2017-01-21 Made the 'avoid objects' AI behavior change direction if the robot is going straight since several seconds.
    [Artificial_Intelligence_Avoid_Objects.c]
2017-05-08 Automated distance measuring to avoid hanging artificial intelligence algorithm loops with unpredictable delays.
    [Artificial_Intelligence.c, Artificial_Intelligence_Avoid_Objects.c, Distance_Sensor.c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]
2017-05-08 Added 'escaping' capability when an object comes too close during the 'follow object' behaviour.
    [Artificial_Intelligence_Follow_Objects.c]
2020-09-05 Added chassis construction pictures and brief instructions to README.md.
2020-09-05 Moved schematic picture to resources directory.
2020-09-05 Added motors assembly and voltage regulator assembly pictures and instructions to README.md.
2020-09-05 Added chassis upper part assembly pictures and instructions to README.md.
2020-09-05 Added electronic board pictures to README.md.
2020-09-05 Added fully assembled robot pictures to README.md.
